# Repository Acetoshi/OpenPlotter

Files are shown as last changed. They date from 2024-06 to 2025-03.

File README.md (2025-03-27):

# OpenPlotter
An open source machine for plotting stuff, this repo is still a work in progress, more parts and drawings will soon be uploaded. 
[Mechanical source files](https://cad.onshape.com/documents/46722cd283d12a82f0ec8435/w/54065c5dafbb0bb403c8ca67/e/3b850448fa15e10835d7a433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) are available. 

Feel free to open an issue if you encounter any problem. 

# Tools required
- 3D Printer
- M6 Tap wrench
- M3, M5, M6 allen Keys
- Soldering iron
- Metal saw
- Power drill + 7mm Metal drill bit

# Bill of materials

## Nuts'n'Bolts Needed

- M3x10mm Hex screws (x50)
- M3 nuts (x8)
- M3 T-Slot nuts (x50)
- M5x8mm Hex screws (x30)
- M5x25mm Hex screws (x10)
- M5x40mm Hex screws (x3)
- M5 Nut (x15)
- M5 T-Slot nuts (x50)
- M6x10mm Hex screws (x6)
- M6x18mm Hex screws (x3)
- M6x35mm Hex screws (x8)
- M5 Wing nuts (x2)
- M3 Nut (x15)
- M6 Washer (x8)

## Aluminium profiles
### 2040 V-slot
- 1000mm (x2)
- 850mm (x1) 

### 2020 V-slot
- 828mm (x1)
- 360mm (x2)
- 190mm (x2)
- 170mm (x2)
- 80mm (x2)
- 60mm (x2)

### 6mm round tube 
- 85 mm (x1)
- 75 mm (x1)

## Other Mechanical parts
- NEMA 17 stepper motor (x4)
- GT2 20Teeth Idler Pulley Bore 5mm (x5)
- GT2 20Teeth Pulley Bore 5mm (x4)
- GT2 6mm wide timing belt (6m minimum)
- OpenBuilds V-Slot Gantry Kits 20 mm (x3) [These little guys](https://openbuildspartstore.com/v-slot-gantry-kit-20mm/)
- 10 x 10 x 1000 mm Cable chain (x2) [Like this one](https://www.amazon.fr/chudian-10mmx10mm-Transporteur-Imprimante-Machine%EF%BC%8CNoir/dp/B07Y6769LL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)
- PETG 3D printing filament compatible with your printer (1kg)
- 15 x 840 x 1000 mm piece of MDF board
- zipTies : a lot

## Electronics
- Arduino UNO (x1)
- Arduino CNC Shield V3 (x1)
- Stepstick A4988 - Stepper motor driver (x4)
- 150W(mini) 24V Power Supply (x1)
- A fan to keep the drivers cool

# Software

This machine uses [GRBL](https://github.com/gnea/grbl) as a firmware, the configuration file is in the software folder. 
In order to send G-code to the machine we use [Universal G-Code Sender](https://winder.github.io/ugs_website/) on a laptop. 

Installation instructions for linux can be found [here](https://github.com/Acetoshi/OpenPlotter/blob/main/Software/LINUX_INSTALL_STEPS.md)

To create Gcode i use [this extension](https://github.com/Acetoshi/gcodetools-for-GRBL-Pen-Plotter) with [Inkscape](https://inkscape.org), which is adapted to this machine's GRBL config

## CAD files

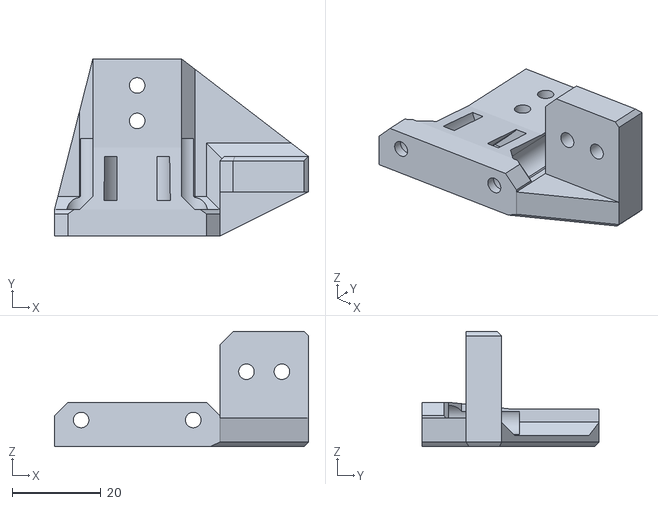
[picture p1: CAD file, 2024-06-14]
3D Printed Parts/X axis - CableChain Mount.stl
57.3 x 40.0 x 26.0

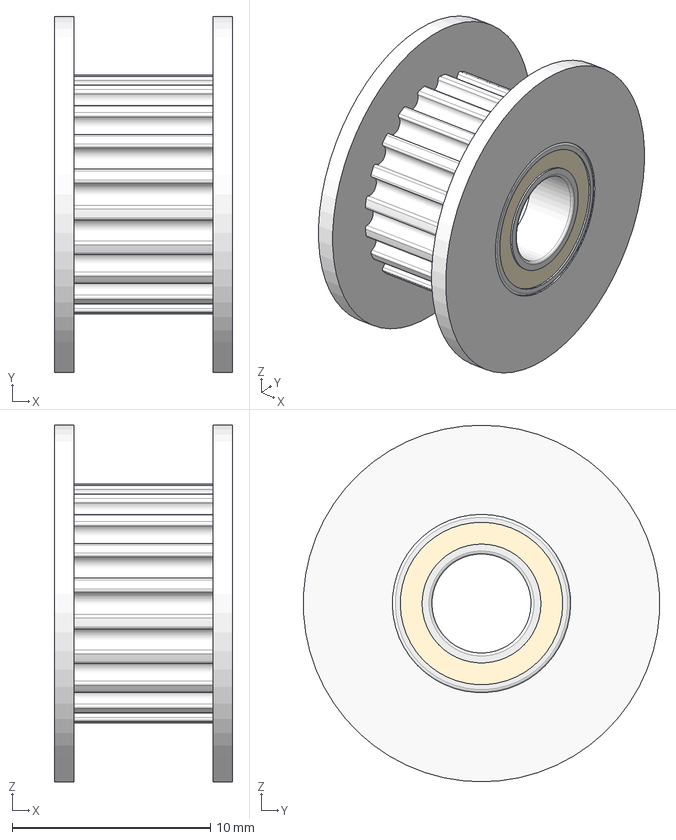
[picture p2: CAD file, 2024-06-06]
Mechanical Parts/idler pulley GT2 20T B5.step
9.00 x 18.0 x 18.0 mm

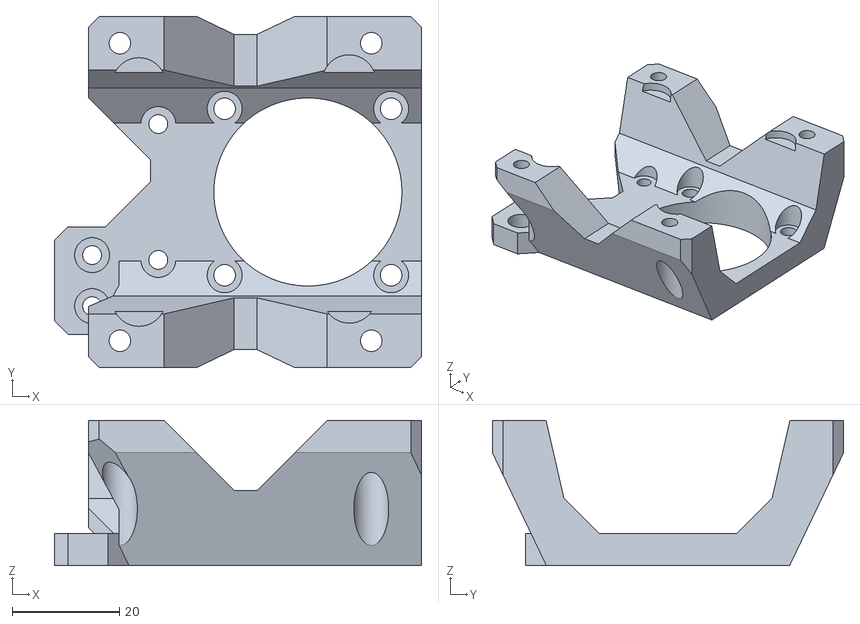
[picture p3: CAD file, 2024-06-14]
3D Printed Parts/X axis - Motor Mounting Bracket.stl
68.3 x 65.4 x 27.0

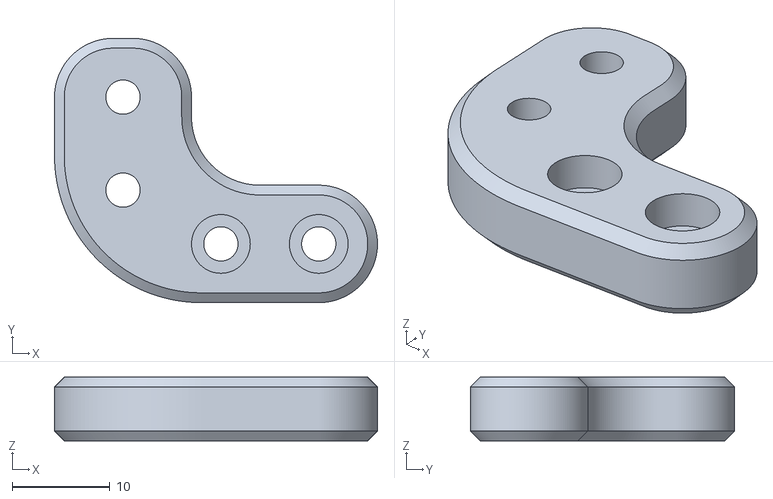
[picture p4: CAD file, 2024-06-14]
3D Printed Parts/Y axis - EndStop Mount.stl
33.0 x 27.0 x 6.50

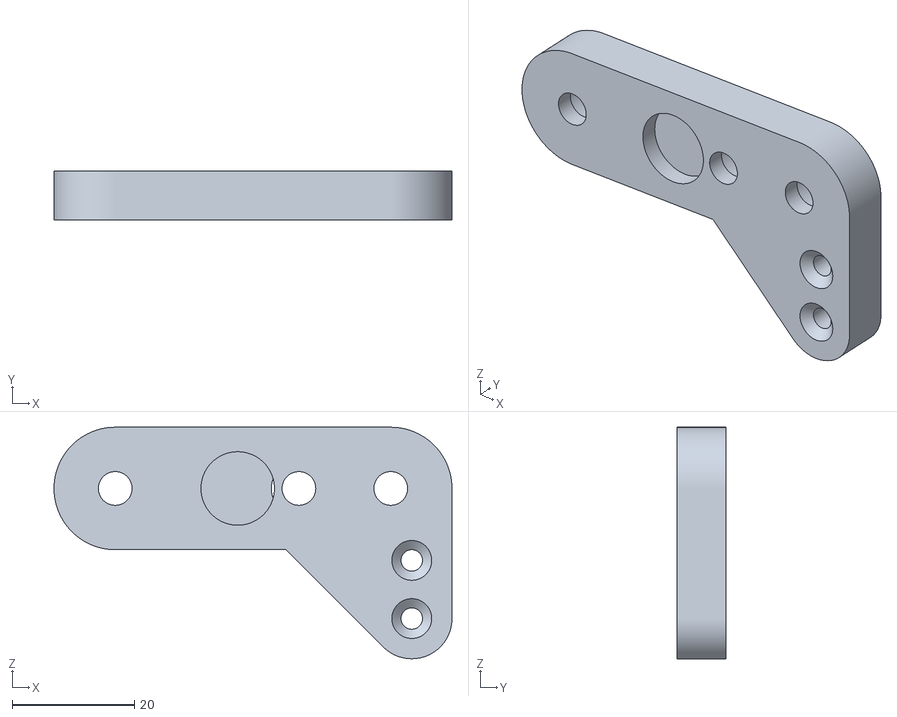
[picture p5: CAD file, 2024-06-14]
3D Printed Parts/X axis - EndStop Mount.stl
65.0 x 8.00 x 37.8

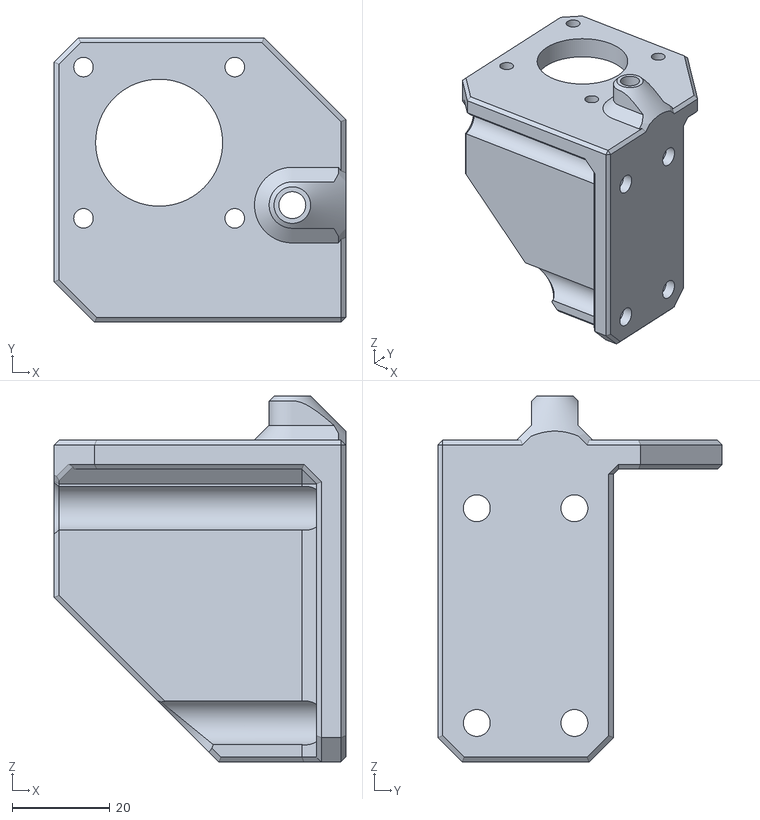
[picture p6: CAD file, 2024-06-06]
3D Printed Parts/Y axis - Right Motor Mounting Bracket.stl
59.7 x 58.3 x 75.0

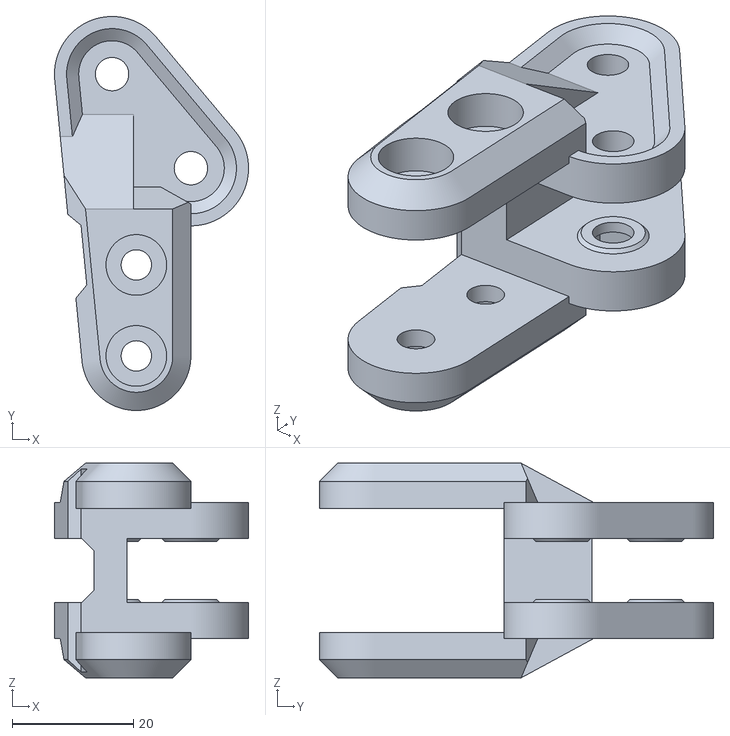
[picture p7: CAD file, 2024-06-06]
3D Printed Parts/Y axis - Idler Pulleys Holder.stl
32.0 x 65.0 x 35.4

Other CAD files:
3D Printed Parts/Y axis - Left Motor Mounting Bracket.stl

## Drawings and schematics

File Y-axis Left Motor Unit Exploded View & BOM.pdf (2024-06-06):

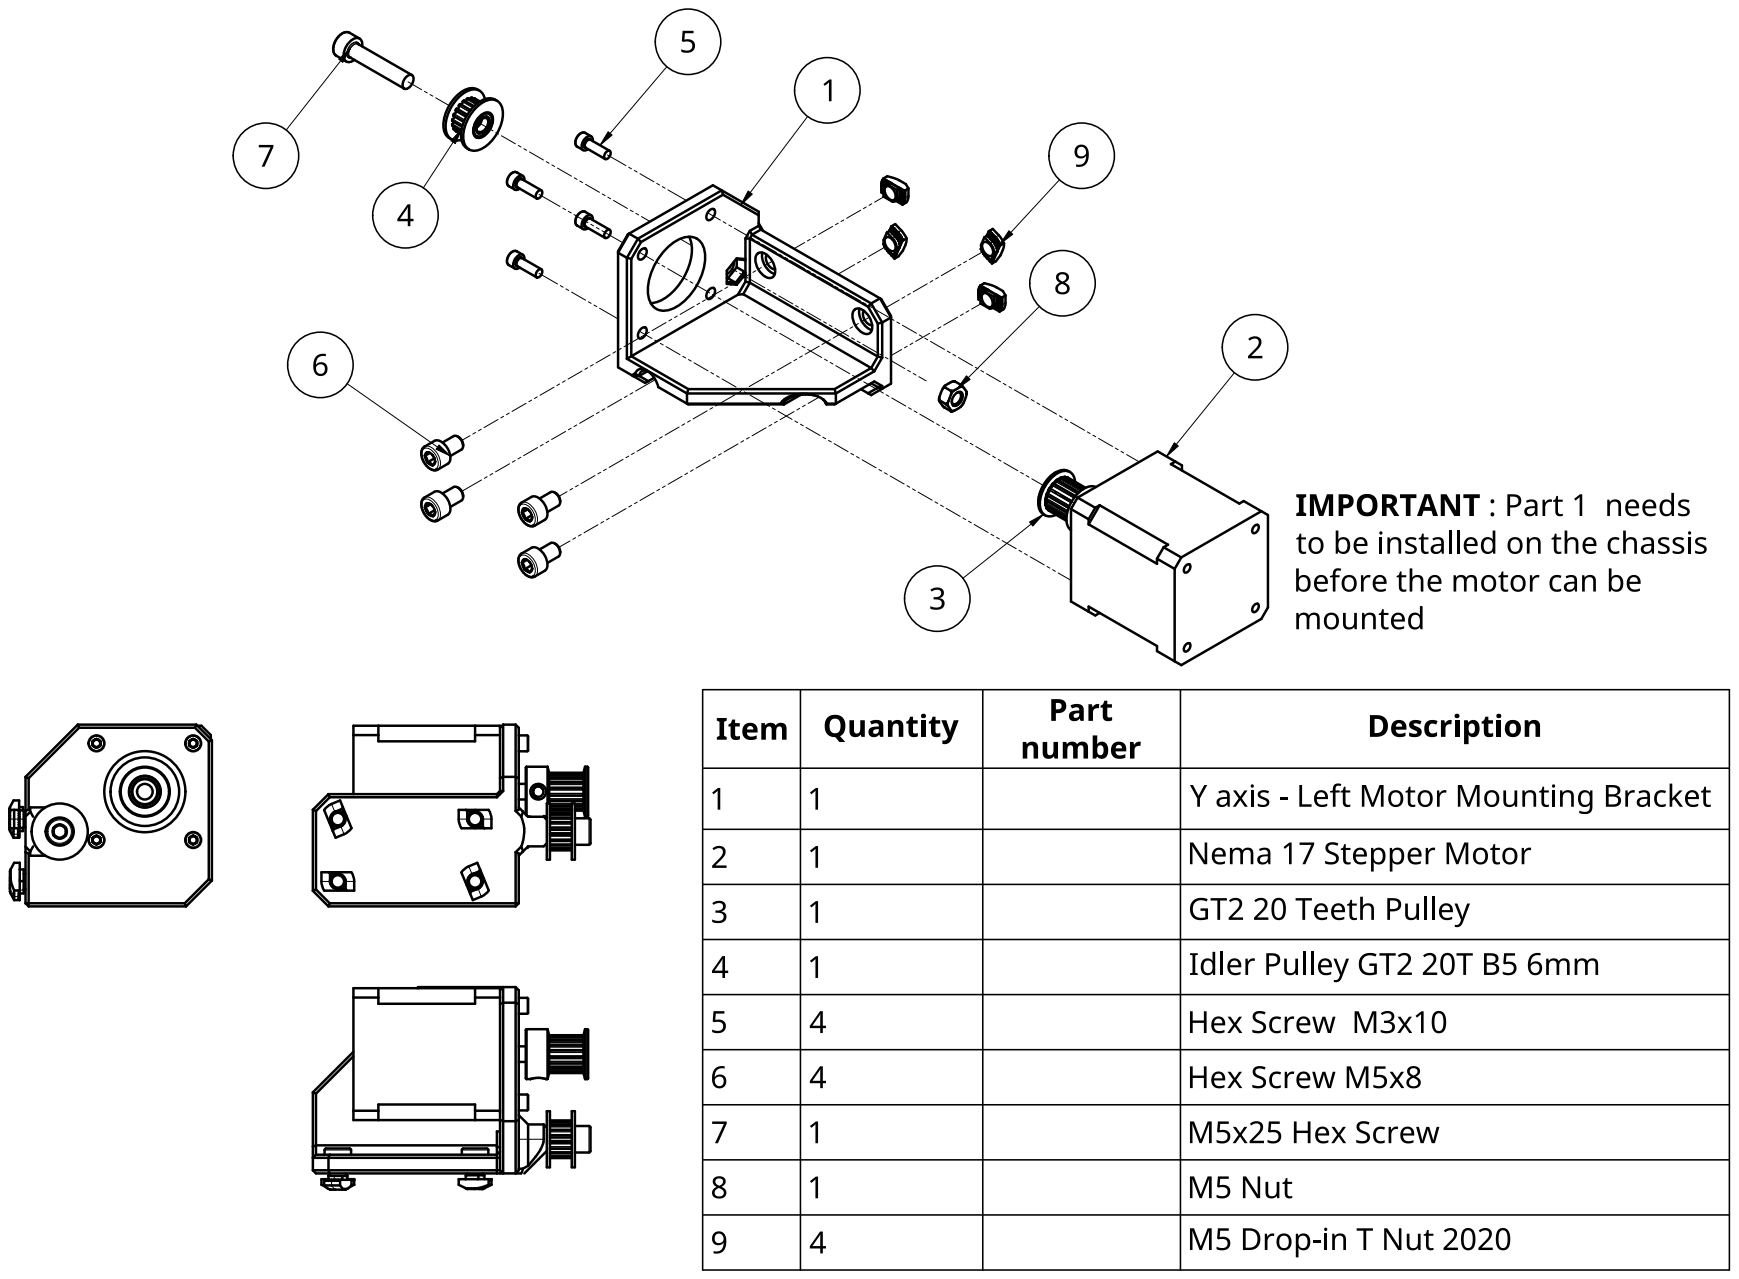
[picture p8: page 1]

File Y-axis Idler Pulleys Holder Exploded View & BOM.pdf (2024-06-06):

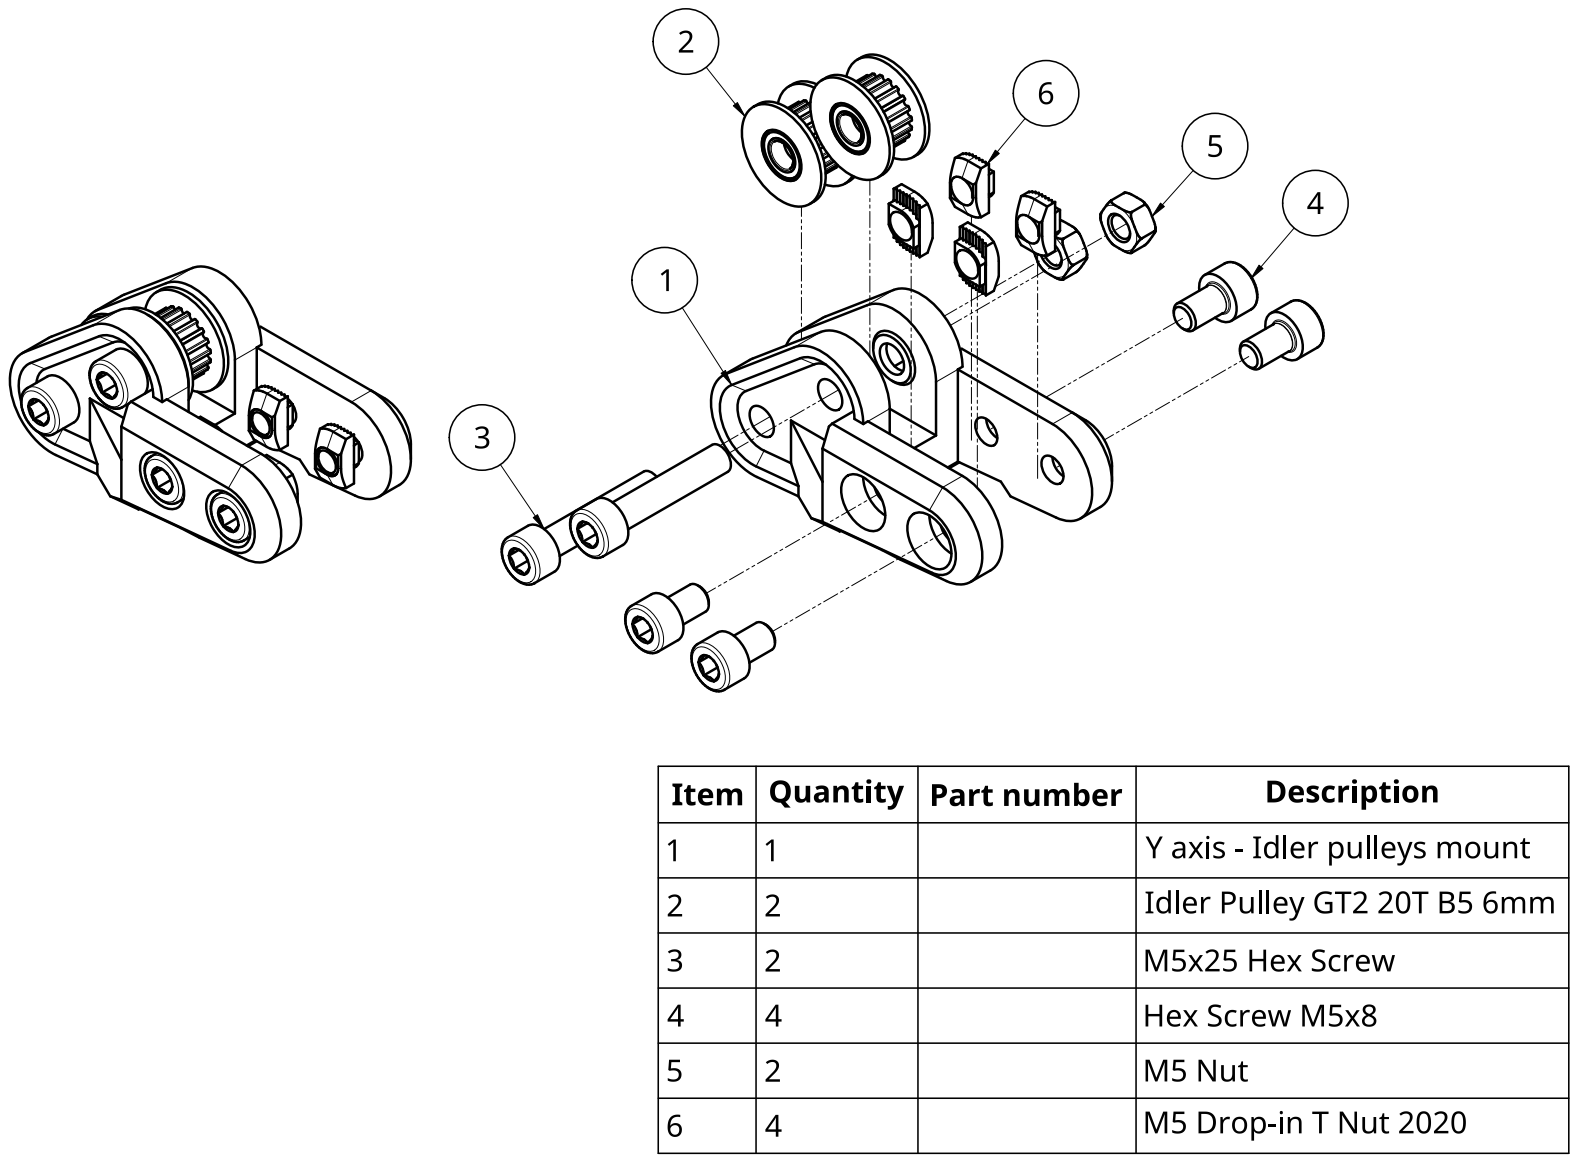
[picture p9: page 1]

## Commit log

2024-06-06 modified Y pulleys holder to fit standard GT2 20T 6mm pulleys, and made a drawing
    [Y axis - Idler Pulleys Holder.stl, idler pulley GT2 20T B5.step]
2024-06-06 made modifications to Y axis motor mounts and drawn BOM accordingly
    [Y axis - Left Motor Mounting Bracket.stl, Y axis - Right Motor Mounting Bracket.stl]
2024-06-14 added endtop mount and X axis carriage
    [X axis - CableChain Mount.stl, X axis - Motor Mounting Bracket.stl, Y axis - EndStop Mount.stl]
2024-06-14 added endtop mount for X axis
    [X axis - EndStop Mount.stl, X axis - Motor Mounting Bracket.stl, Y axis - EndStop Mount.stl]
2024-07-15 added pulley and cablechains to README.md
2024-07-15 added gantry kits to README.md
